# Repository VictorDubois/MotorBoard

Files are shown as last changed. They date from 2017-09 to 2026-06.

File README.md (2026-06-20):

Custom PCB for Krabi V1, to control DC motors using [LMD18200](https://www.ti.com/lit/ds/symlink/lmd18200.pdf)

MCU: [STM32 NUCLEO-G431KB](https://www.st.com/en/evaluation-tools/nucleo-g431kb.html), code is here https://github.com/VictorDubois/Motor-board-STM32-CAN/tree/commit-all

[Click for online viewer</br>
Capture d’écran du 2026-06-20 12-18-06](https://kicanvas.org/?repo=https%3A%2F%2Fgithub.com%2FVictorDubois%2FMotorBoard%2Ftree%2Fv2026.1%2F)

Note: Krabi V2 uses this PCB instead https://github.com/VictorDubois/CanMotorBoard

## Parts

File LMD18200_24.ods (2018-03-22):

Qty | Value | Device | Package | code RS | URL RS | prix unit HT RS (pour 3 boards) |  |  | Prix / carte | code RS particuliers
1 |  | MA03-2 | MA03-2 |  |  |  |  |  | 0
3 |  | MA06-1 | MA06-1 |  |  |  |  |  | 0
2 |  | MA08-1 | MA08-1 |  |  |  |  |  | 0
1 |  | MA10-2 | MA10-2 |  |  |  |  |  | 0
2 | 10k | R | R0805 | 707-7745 | http://fr.rs-online.com/web/p/resistances-traversantes/7077745/ | 0,006 |  |  | 0,015 | 707-7745
5 | 10k | R-EU_R0805 | R0805 | 125-1189 | http://fr.rs-online.com/web/p/resistances-cms/1251189/ | 0,002 | CRG0805F10K |  | 0,0125 | 707-7745
3 |  | W237-102 | W237-102 | 897-1262 + 897-1219 | http://fr.rs-online.com/web/p/borniers-pour-ci/8971262/ | 0,534 |  | + http://fr.rs-online.com/web/p/borniers-pour-ci/8971219/ | 2,0025 | 897-1262 + 897-1219
1 | 0R | R | R0805 | 125-1187 | http://fr.rs-online.com/web/p/resistances-cms/1251187/ | 0,002 | CRG0805ZR |  | 0,0025 | 901-3664
2 | 0R | R-EU_R0805 | R0805 | 125-1187 | http://fr.rs-online.com/web/p/resistances-cms/1251187/ | 0,002 | CRG0805ZR |  | 0,005 | 901-3664
2 | 1000mF | CPOL-EUE5-13 | E5-13 | 315-0754 | http://fr.rs-online.com/web/p/condensateurs-aluminium/3150754/ | 0,446 | EEUFC1V102 |  | 1,115 | 7111321
1 | 100nF | C-EUC0805 | C0805 | 264-4416 | http://fr.rs-online.com/web/p/condensateurs-ceramique-multicouche/2644416/ | 0,029 | C0805C104K5RACTU |  | 0,03625
6 | 100nF | C2.5/2 | C2.5-2 | 852-3273 | http://fr.rs-online.com/web/p/condensateurs-ceramique-multicouche/8523273/ | 0,02 | K104K15X7RF53L2 |  | 0,15 | 8523302 (https://www.rs-particuliers.com/WebCatalog/Condensateur_ceramique_multicouche_MLCC__Traversant__100nF___20___80__100V_dc__dielectrique__Y5V-8523302.aspx)
4 | 10nF | C2.5/2 | C2.5-2 | 264-4371 | http://fr.rs-online.com/web/p/condensateurs-ceramique-multicouche/2644371/ | 0,019 | C0805C103K5RACTU |  | 0,095 | 6994995 (https://www.rs-particuliers.com/WebCatalog/Condensateur_ceramique_multicouche_MLCC__Traversant__10nF__±20__100V_dc__dielectrique__Z5U-6994995.aspx)
1 | 30V | ZENER-DIODESOD80C | SOD80C |  |  |  |  |  | 0
2 | 330nF | C2.5/2 | C2.5-2 | 379-094 | http://fr.rs-online.com/web/p/condensateurs-ceramique-multicouche/0379094/ | 0,203 | FK24X7R1H334K |  | 0,5075 | 699-5153 (https://fr.rs-online.com/web/p/condensateurs-ceramique-multicouche/6995153/)
6 | 390 | R-EU_R0805 | R0805 | 679-1327 | http://fr.rs-online.com/web/p/resistances-cms/6791327/ | 0,009 | CRCW0805392RFKEA |  | 0,0675 | 679-1327
1 | 5V | ZENER-DIODESOD80C | SOD80C |  |  |  |  |  | 0
1 | 7406D | 7406D | SO14 | 662-7424 | http://fr.rs-online.com/web/p/buffers-et-drivers-de-ligne/6627424/ | 0,4 | SN7406DR |  | 0,5 | 662-7424
1 | 74HCT541DW | 74HCT541DW | SO20W | 177-6887 | http://fr.rs-online.com/web/p/buffers-et-drivers-de-ligne/1776887/ | 0,54 | 74HCT541D |  | 0,675 | 177-6887
1 | 7805TV | 7805TV | TO220V | 298-8508 | http://fr.rs-online.com/web/p/regulateurs-de-tension-lineaires/2988508/ | 0,29 | L7805ACV |  | 0,3625 | 298-8508
1 | ADC08032D | ADC08032D | SO08 | 669-6058 | http://fr.rs-online.com/web/p/can-a-usage-general/6696058/ | 1,615 | MCP3002-I/SN |  | 2,01875 | 669-6058 | Le 13/12/17
5 | HCPL2630 | HCPL2630 | DIL08 | 671-1419 | http://fr.rs-online.com/web/p/optocoupleurs/6711419/ | 2,07 | HCPL2630 |  | 12,9375 | 671-1419
2 | LM18200T | LM18200T | TO-220-11 | 534-4276 | http://fr.rs-online.com/web/p/drivers-de-moteur/5344276/ | 14,17 | LMD18200T/NOPB |  | 35,425 | 534-4276
4 | MOUNT-PAD-ROUND3.2 | MOUNT-PAD-ROUND3.2 | 3,2-PAD |  |  |  |  |  | 0
2 | NC | R-EU_R0805 | R0805 |  |  |  |  |  | 0
 |  |  |  |  |  |  |  |  | 55,9275

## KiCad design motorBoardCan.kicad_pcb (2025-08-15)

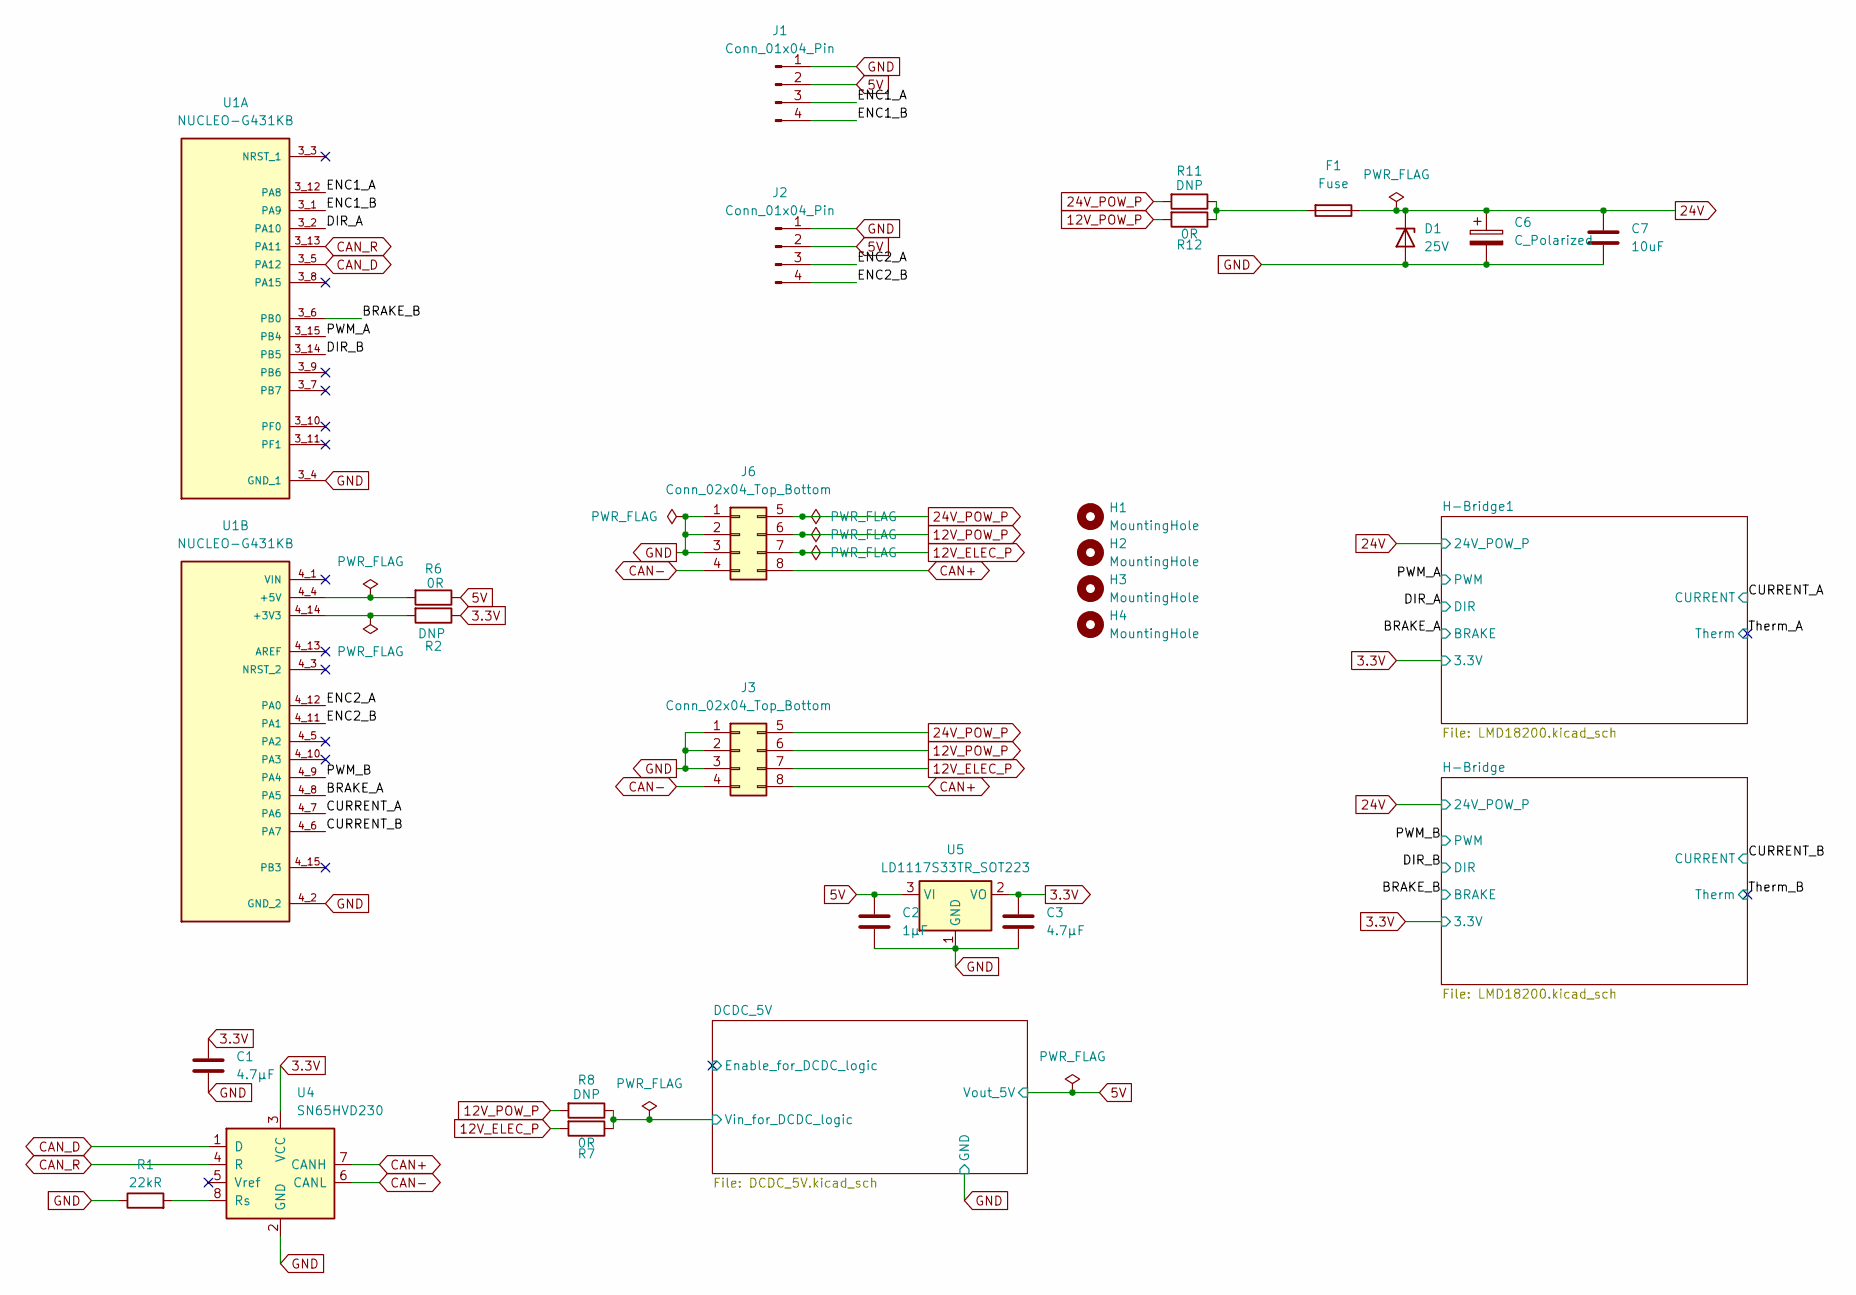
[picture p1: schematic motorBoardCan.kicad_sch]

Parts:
C1, C3: 4.7µF; C_1206_3216Metric; LCSC# C29823
C2: 1µF; C_1206_3216Metric; LCSC# C91151
C6: C_Polarized; CP_Radial_D10.0mm_P5.00mm; LCSC# C398835
C7: 10uF; C_0805_2012Metric; LCSC# C1713
D1: 25V; C_0805_2012Metric; LCSC# C118721
F1: Fuse; Fuse_Littelfuse-NANO2-451_453; LCSC# C27515
H1, H2, H3, H4: MountingHole; MountingHole_3.2mm_M3
J1, J2: Conn_01x04_Pin; PinHeader_1x04_P2.54mm_Vertical; LCSC# C2691448
J3, J6: Conn_02x04_Top_Bottom; Molex_Micro-Fit_3.0_43045-0812_2x04_P3.00mm_Vertical; LCSC# C277661
R1: 22kR; R_0603_1608Metric; LCSC# C2907128
R2, R8, R11: DNP; R_0603_1608Metric
R6, R7, R12: 0R; R_0603_1608Metric; LCSC# C21189
U1: NUCLEO-G431KB; MODULE_NUCLEO-G431KB
U4: SN65HVD230; SOIC-8_3.9x4.9mm_P1.27mm; LCSC# C12084
U5: LD1117S33TR_SOT223; SOT-223-3_TabPin2; LCSC# C20538890

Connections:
3.3V: C1.1, C3.1, R2.1, U4.3 (VCC), U5.2 (VO); also elsewhere on the board
5V: C2.1, J1.2, J2.2, R6.1, U5.3 (VI); also elsewhere on the board
12V_ELEC_P: J3.7, J6.7, R7.2
12V_POW_P: J3.6, J6.6, R8.2, R12.2
24V: C6.1, C7.1, D1.1 (K), F1.1; also elsewhere on the board
24V_POW_P: J3.5, J6.5, R11.2
/BRAKE_A: U1.4_8 (PA5); also elsewhere on the board
/BRAKE_B: U1.3_6 (PB0); also elsewhere on the board
/CURRENT_A: U1.4_7 (PA6); also elsewhere on the board
/CURRENT_B: U1.4_6 (PA7); also elsewhere on the board
/DCDC_5V/Vin_for_DCDC_logic: R7.1, R8.1; also elsewhere on the board
/DIR_A: U1.3_2 (PA10); also elsewhere on the board
/DIR_B: U1.3_14 (PB5); also elsewhere on the board
/ENC1_A: J1.3, U1.3_12 (PA8)
/ENC1_B: J1.4, U1.3_1 (PA9)
/ENC2_A: J2.3, U1.4_12 (PA0)
/ENC2_B: J2.4, U1.4_11 (PA1)
/PWM_A: U1.3_15 (PB4); also elsewhere on the board
/PWM_B: U1.4_9 (PA4); also elsewhere on the board
CAN+: J3.8, J6.8, U4.7 (CANH)
CAN-: J3.4, J6.4, U4.6 (CANL)
CAN_D: U1.3_5 (PA12), U4.1 (D)
CAN_R: U1.3_13 (PA11), U4.4 (R)
GND: C1.2, C2.2, C3.2, C6.2, C7.2, D1.2 (A), J1.1, J2.1, J3.1, J3.2, J3.3, J6.1, J6.2, J6.3, R1.1, U1.3_4 (GND_1), U1.4_2 (GND_2), U4.2 (GND), U5.1 (GND); also elsewhere on the board
unnamed: F1.2, R11.1, R12.1
unnamed: R2.2, U1.4_14 (+3V3)
unnamed: R6.2, U1.4_4 (+5V)
unnamed: R1.2, U4.8 (Rs)

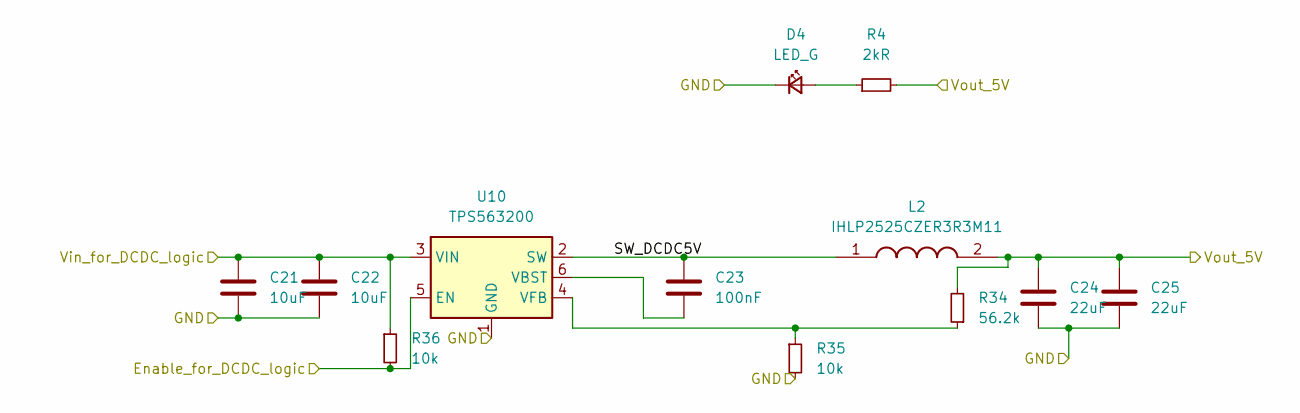
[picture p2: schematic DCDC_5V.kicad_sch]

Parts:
C21, C22: 10uF; C_0805_2012Metric; LCSC# C1713
C23: 100nF; C_0603_1608Metric; LCSC# C14663
C24, C25: 22uF; C_0805_2012Metric; LCSC# C5674
D4: LED_G; LED_0805_2012Metric; LCSC# C965815
L2: IHLP2525CZER3R3M11; INDPM6965X300N; Mouser Part Number 70-IHLP2525CZER3R3M1
R4: 2kR; R_0603_1608Metric; LCSC# C2907137
R34: 56.2k; C_0603_1608Metric; LCSC# C2930117
R35, R36: 10k; C_0603_1608Metric; LCSC# C2930027
U10: TPS563200; SOT-23-6; LCSC# C97253

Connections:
5V: C24.1, C25.1, L2.2, R4.2, R34.2; also elsewhere on the board
/DCDC_5V/Enable_for_DCDC_logic: R36.2, U10.5 (EN)
/DCDC_5V/SW_DCDC5V: C23.1, L2.1, U10.2 (SW)
/DCDC_5V/Vin_for_DCDC_logic: C21.1, C22.1, R36.1, U10.3 (VIN); also elsewhere on the board
GND: C21.2, C22.2, C24.2, C25.2, D4.1 (K), R35.2, U10.1 (GND); also elsewhere on the board
unnamed: D4.2 (A), R4.1
unnamed: C23.2, U10.6 (VBST)
unnamed: R34.1, R35.1, U10.4 (VFB)

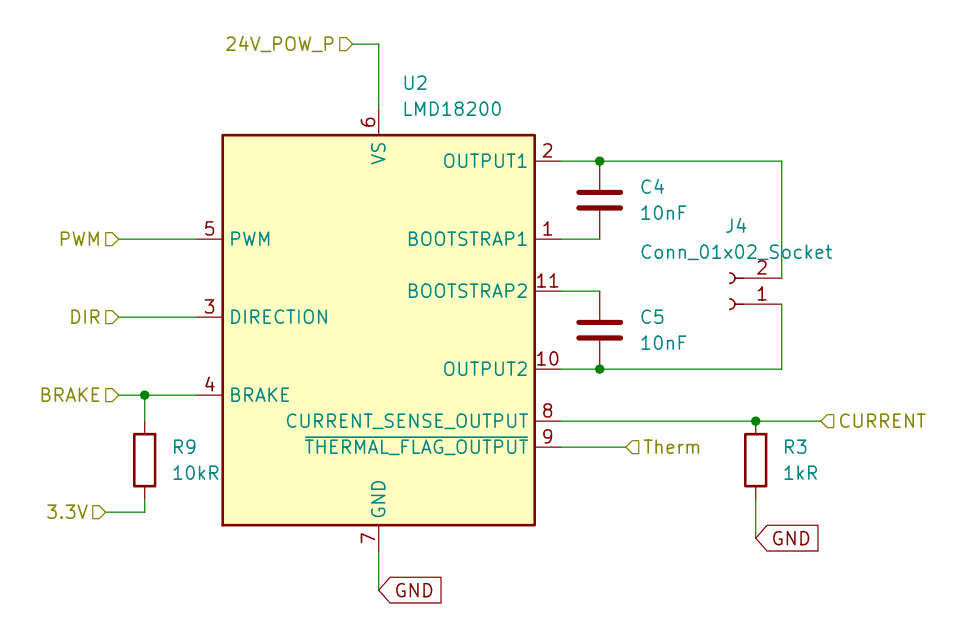
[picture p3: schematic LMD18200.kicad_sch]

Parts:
C4, C5: 10nF; C_0603_1608Metric; LCSC# C57112
J4: Conn_01x02_Socket; PhoenixContact_MC_1,5_2-G-3.81_1x02_P3.81mm_Horizontal
R3: 1kR; R_0603_1608Metric; LCSC# C2907113
R9: 10kR; R_0603_1608Metric; LCSC# C2907113
U2: LMD18200; TO-220-11_P3.4x5.08mm_StaggerOdd_Lead4.85mm_Vertical; LCSC# C117011

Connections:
3.3V: R9.1; also elsewhere on the board
24V: U2.6 (VS); also elsewhere on the board
/BRAKE_B: R9.2, U2.4 (BRAKE); also elsewhere on the board
/CURRENT_B: R3.2, U2.8 (CURRENT_SENSE_OUTPUT); also elsewhere on the board
/DIR_B: U2.3 (DIRECTION); also elsewhere on the board
/PWM_B: U2.5 (PWM); also elsewhere on the board
/Therm_B: U2.9 (~THERMAL_FLAG_OUTPUT)
GND: R3.1, U2.7 (GND); also elsewhere on the board
unnamed: C5.2, J4.1, U2.10 (OUTPUT2)
unnamed: C4.1, J4.2, U2.2 (OUTPUT1)
unnamed: C4.2, U2.1 (BOOTSTRAP1)
unnamed: C5.1, U2.11 (BOOTSTRAP2)

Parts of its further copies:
C8, C9: 10nF; C_0603_1608Metric; LCSC# C57112
J5: Conn_01x02_Socket; PhoenixContact_MC_1,5_2-G-3.81_1x02_P3.81mm_Horizontal
R5: 1kR; R_0603_1608Metric; LCSC# C2907113
R10: 10kR; R_0603_1608Metric; LCSC# C2907113
U6: LMD18200; TO-220-11_P3.4x5.08mm_StaggerOdd_Lead4.85mm_Vertical; LCSC# C117011

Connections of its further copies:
3.3V: R10.1; also elsewhere on the board
24V: U6.6 (VS); also elsewhere on the board
/BRAKE_A: R10.2, U6.4 (BRAKE); also elsewhere on the board
/CURRENT_A: R5.2, U6.8 (CURRENT_SENSE_OUTPUT); also elsewhere on the board
/DIR_A: U6.3 (DIRECTION); also elsewhere on the board
/PWM_A: U6.5 (PWM); also elsewhere on the board
/Therm_A: U6.9 (~THERMAL_FLAG_OUTPUT)
GND: R5.1, U6.7 (GND); also elsewhere on the board
unnamed: C9.2, J5.1, U6.10 (OUTPUT2)
unnamed: C8.1, J5.2, U6.2 (OUTPUT1)
unnamed: C8.2, U6.1 (BOOTSTRAP1)
unnamed: C9.1, U6.11 (BOOTSTRAP2)

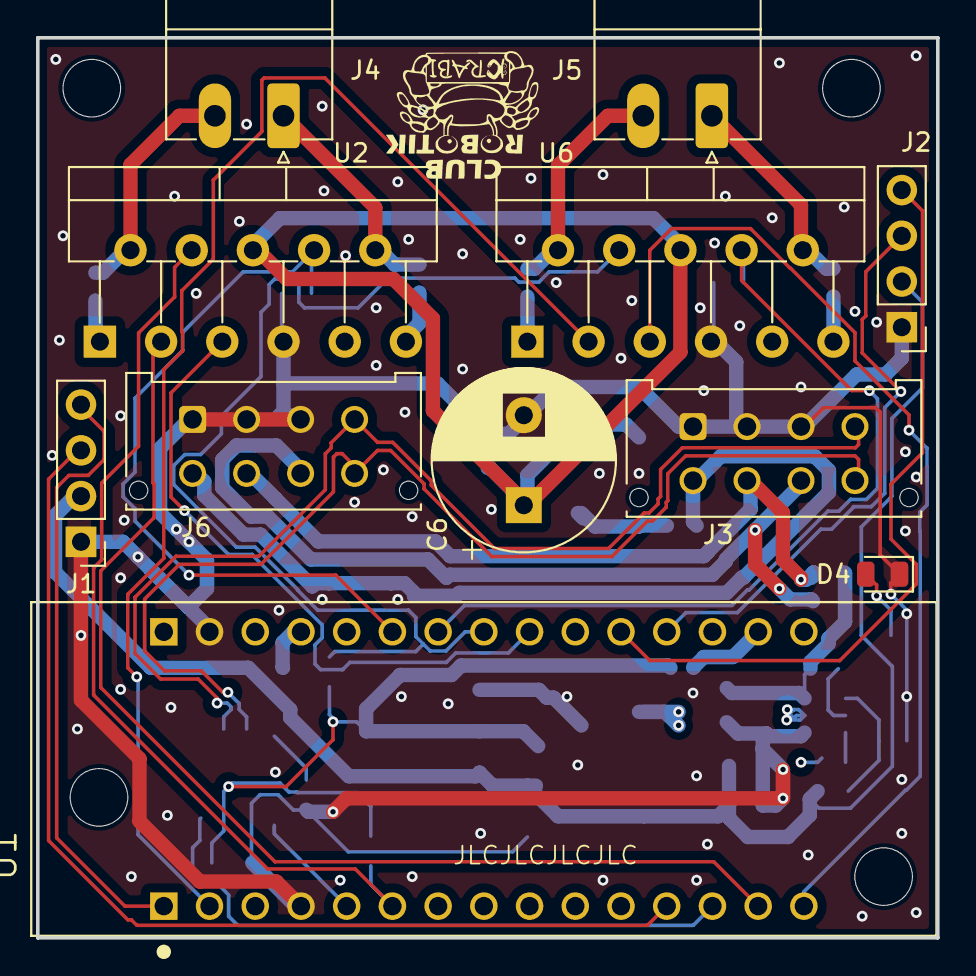
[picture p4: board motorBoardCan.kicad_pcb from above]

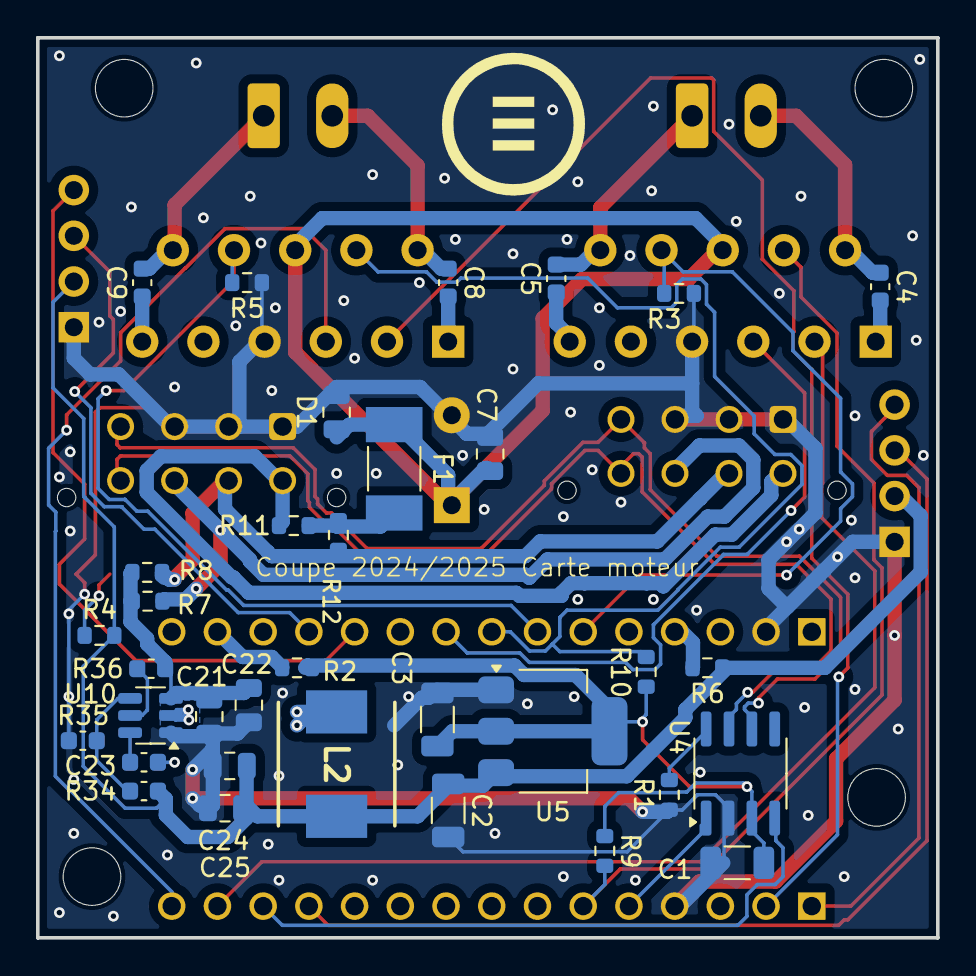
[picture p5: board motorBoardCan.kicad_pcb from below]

Board: 6 copper layers, 50.0 x 50.0 mm, 49 parts (34 on the bottom side), 41 nets.

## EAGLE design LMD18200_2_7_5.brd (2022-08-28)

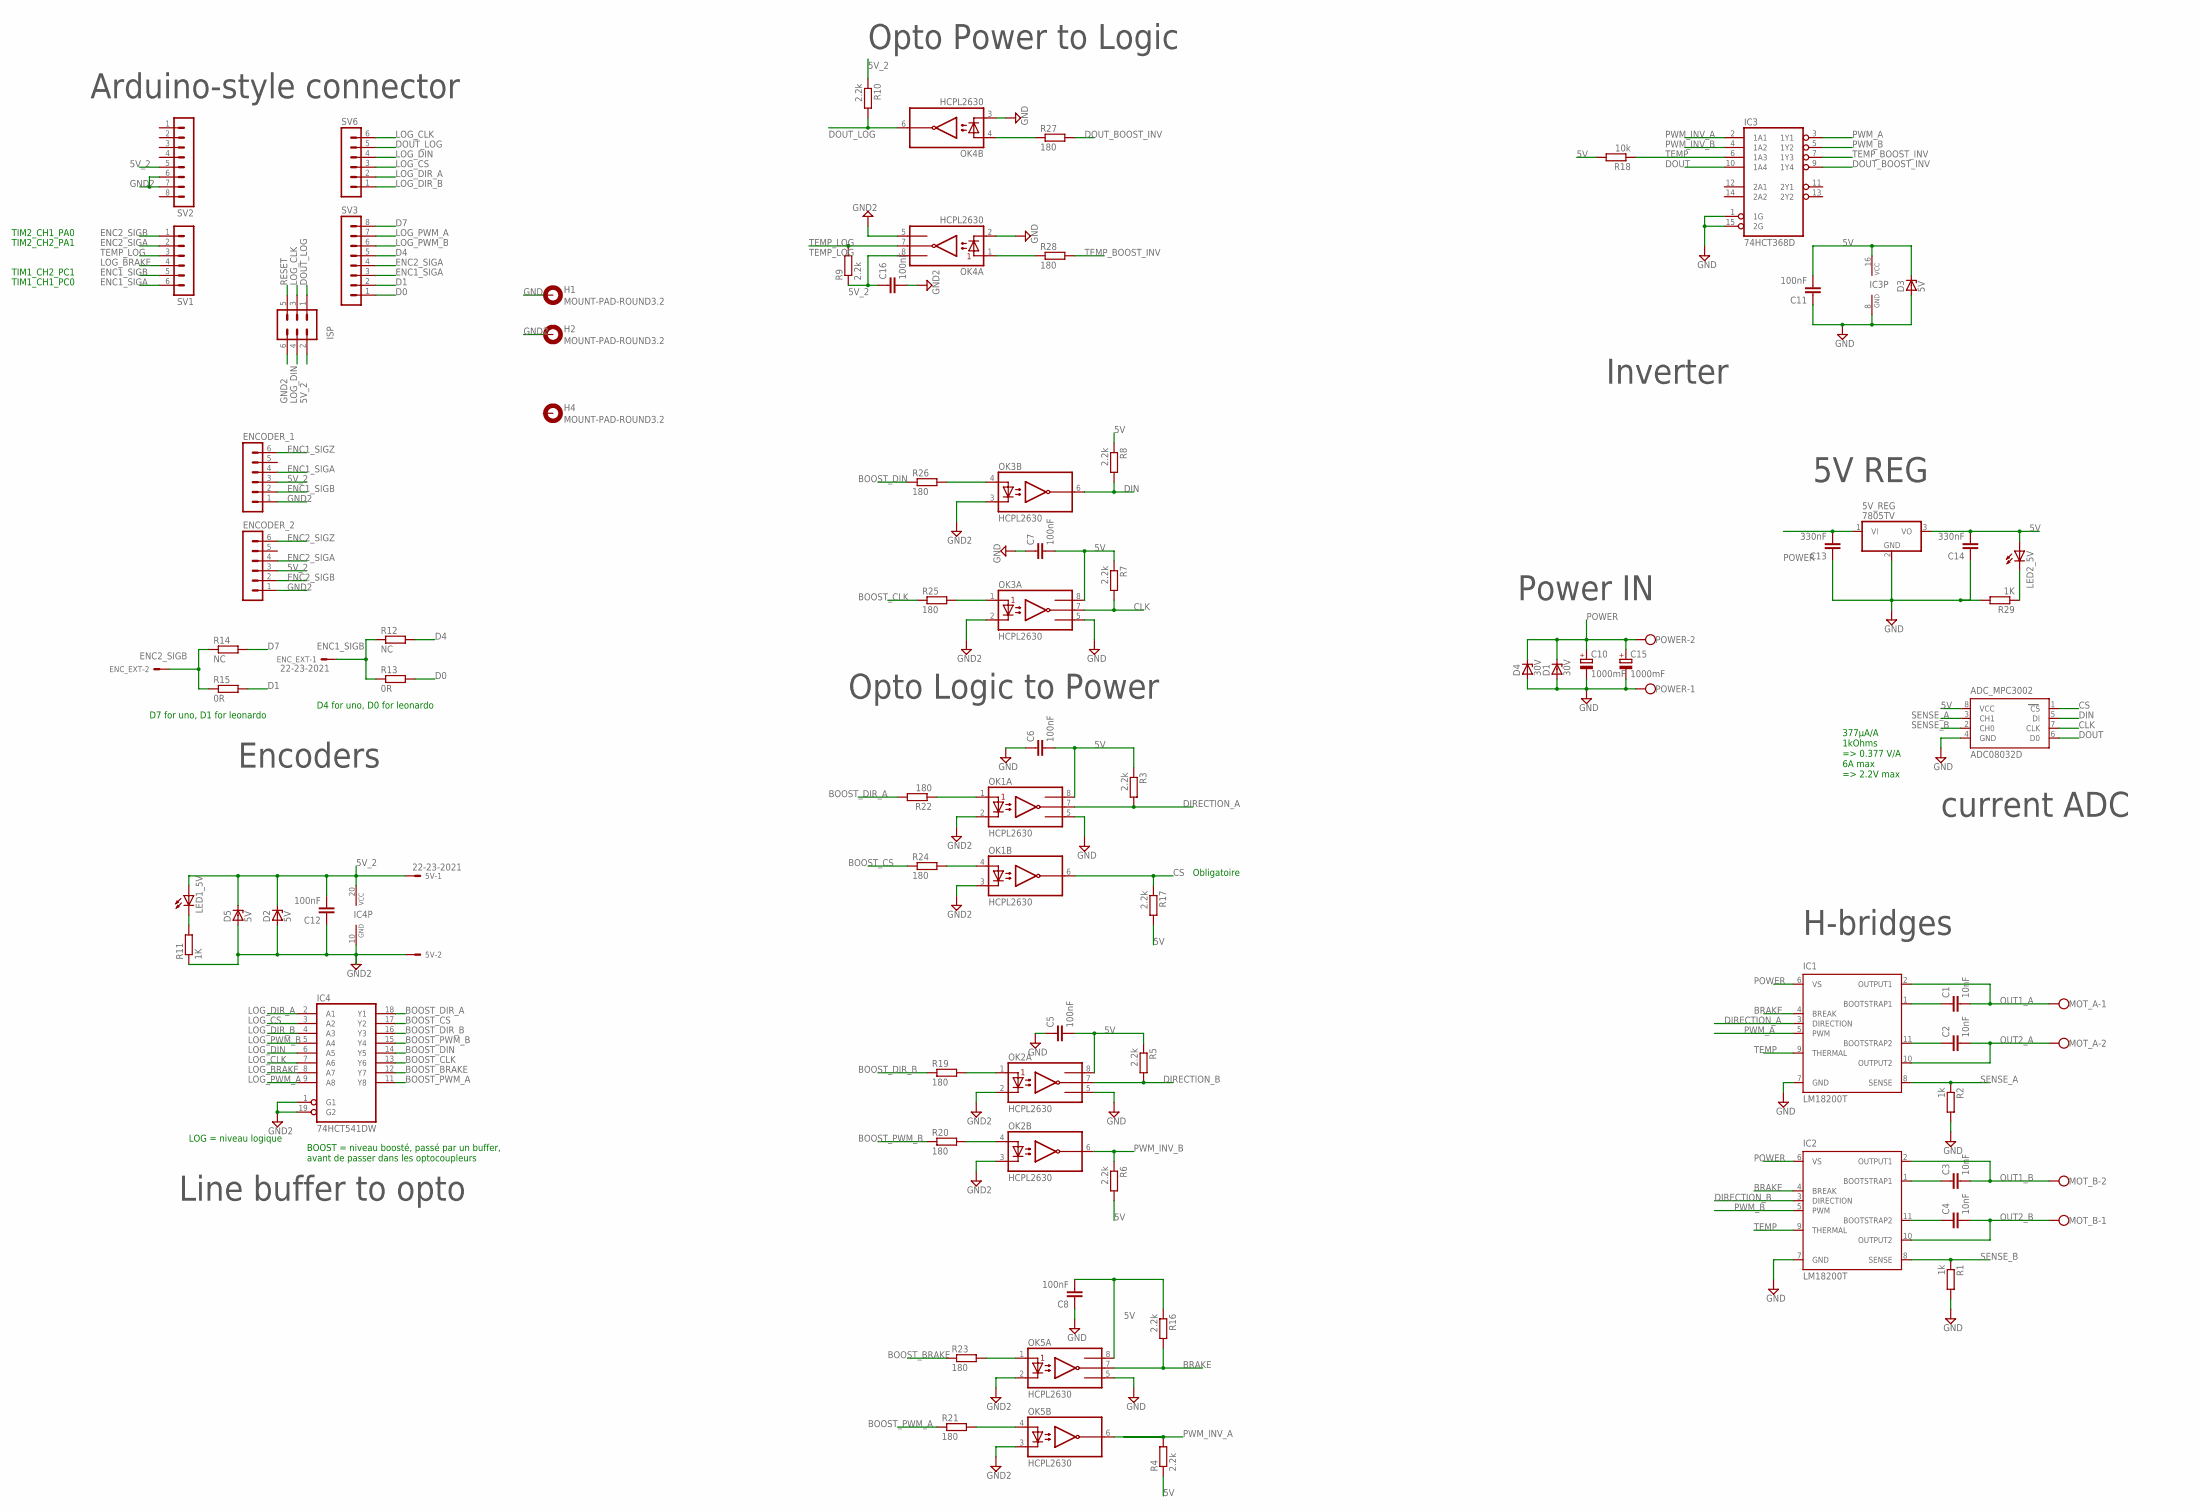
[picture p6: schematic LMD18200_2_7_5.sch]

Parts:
5V: 22-23-2021
5V_REG: 7805TV; TO220V
ADC_MPC3002: ADC08032D; SO08
C1, C2, C3, C4: 10nF; C0603
C5, C6, C7, C8, C12, C16: 100nF; C0603
C10, C15: 1000mF; E5-13
C11: 100nF; C0805
C13, C14: 330nF; C0603
D1: 30V; SOD80C
D2: 5V; SOD80C
D3, D5: 5V; DO34Z7
D4: 30V; DO34Z7
ENCODER_1, ENCODER_2: MA06-1
ENC_EXT: 22-23-2021
H1, H2, H4: MOUNT-PAD-ROUND3.2; 3,2-PAD
IC1, IC2: LM18200T; TO-220-11
IC3: 74HCT368D; SO16
IC4: 74HCT541DW; SO20W
ISP: MA03-2
LED1_5V, LED2_5V: LEDSML0805; SML0805
MOT_A: W237-102
MOT_B: W237-102
OK1, OK2, OK3, OK4, OK5: HCPL2630; DIL08
POWER: W237-102
R1, R2: 1k; R0603
R3, R4, R5, R6, R7, R8, R9, R10, R16, R17: 2.2k; R0603
R11, R29: 1K; R0603
R12, R14: NC; R0603
R13, R15: 0R; R0603
R18: 10k; R0603
R19, R20, R21, R22, R23, R24, R25, R26, R27, R28: 180; R0603
SV1, SV6: MA06-1
SV2, SV3: MA08-1

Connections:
5V: 5V_REG.3 (VO), ADC_MPC3002.8 (VCC), C5.2, C6.2, C7.2, C8.2, C11.2, C14.2, D3.C, IC3.16 (VCC), LED2_5V.A, OK1.8 (VCC), OK2.8 (VCC), OK3.8 (VCC), OK5.8 (VCC), R3.1, R4.1, R5.1, R6.2, R7.1, R8.1, R16.1, R17.2, R18.2
5V_2: 5V.1, C12.2, C16.1, D2.C, D5.C, ENCODER_1.3, ENCODER_2.3, IC4.20 (VCC), ISP.2, LED1_5V.A, OK4.8 (VCC), R9.1, R10.1, SV2.5
BOOST_BRAKE: IC4.12 (Y7), R23.1
BOOST_CLK: IC4.13 (Y6), R25.1
BOOST_CS: IC4.17 (Y2), R24.1
BOOST_DIN: IC4.14 (Y5), R26.1
BOOST_DIR_A: IC4.18 (Y1), R22.2
BOOST_DIR_B: IC4.16 (Y3), R19.1
BOOST_OUT1_A: C1.1, IC1.1 (BOOTSTRAP1)
BOOST_OUT1_B: C3.1, IC2.1 (BOOTSTRAP1)
BOOST_OUT2_A: C2.1, IC1.11 (BOOTSTRAP2)
BOOST_OUT2_B: C4.1, IC2.11 (BOOTSTRAP2)
BOOST_PWM_A: IC4.11 (Y8), R21.1
BOOST_PWM_B: IC4.15 (Y4), R20.1
BRAKE: IC1.4 (BREAK), IC2.4 (BREAK), OK5.7 (VO1), R16.2
CLK: ADC_MPC3002.7 (CLK), OK3.7 (VO1), R7.2
CS: ADC_MPC3002.1 (CS), OK1.6 (VO2), R17.1
D0: R13.2, SV3.1
D1: R15.2, SV3.2
D4: R12.2, SV3.5
D7: R14.2, SV3.8
DIN: ADC_MPC3002.5 (DI), OK3.6 (VO2), R8.2
DIRECTION_A: IC1.3 (DIRECTION), OK1.7 (VO1), R3.2
DIRECTION_B: IC2.3 (DIRECTION), OK2.7 (VO1), R5.2
DOUT: ADC_MPC3002.6 (D0), IC3.10 (1A4)
DOUT_BOOST_INV: IC3.9 (1Y4), R27.2
DOUT_LOG: ISP.1, OK4.6 (VO2), R10.2, SV6.5
ENC1_SIGA: ENCODER_1.4, SV1.6, SV3.3
ENC1_SIGB: ENCODER_1.2, ENC_EXT.1, R12.1, R13.1, SV1.5
ENC1_SIGZ: ENCODER_1.6
ENC2_SIGA: ENCODER_2.4, SV1.2, SV3.4
ENC2_SIGB: ENCODER_2.2, ENC_EXT.2, R14.1, R15.1, SV1.1
ENC2_SIGZ: ENCODER_2.6
GND: 5V_REG.2 (GND), ADC_MPC3002.4 (GND), C5.1, C6.1, C7.1, C8.1, C10.-, C11.1, C13.1, C14.1, C15.-, D1.A, D3.A, D4.A, H1.B3,2, IC1.7 (GND), IC2.7 (GND), IC3.1 (1G), IC3.8 (GND), IC3.15 (2G), OK1.5 (GND), OK2.5 (GND), OK3.5 (GND), OK4.2 (C1), OK4.3 (C2), OK5.5 (GND), POWER.1, R1.2, R2.2, R29.2
GND2: 5V.2, C12.1, C16.2, D2.A, D5.A, ENCODER_1.1, ENCODER_2.1, H2.B3,2, IC4.1 (G1), IC4.10 (GND), IC4.19 (G2), ISP.6, OK1.2 (C1), OK1.3 (C2), OK2.2 (C1), OK2.3 (C2), OK3.2 (C1), OK3.3 (C2), OK4.5 (GND), OK5.2 (C1), OK5.3 (C2), R11.1, SV2.6, SV2.7
LED1_SIG: LED1_5V.C, R11.2
LED2_5V_SIG: LED2_5V.C, R29.1
LOG_BRAKE: IC4.8 (A7), SV1.4
LOG_CLK: IC4.7 (A6), ISP.3, SV6.6
LOG_CS: IC4.3 (A2), SV6.3
LOG_DIN: IC4.6 (A5), ISP.4, SV6.4
LOG_DIR_A: IC4.2 (A1), SV6.2
LOG_DIR_B: IC4.4 (A3), SV6.1
LOG_PWM_A: IC4.9 (A8), SV3.7
LOG_PWM_B: IC4.5 (A4), SV3.6
OUT1_A: C1.2, IC1.2 (OUTPUT1), MOT_A.1
OUT1_B: C3.2, IC2.2 (OUTPUT1), MOT_B.2
OUT2_A: C2.2, IC1.10 (OUTPUT2), MOT_A.2
OUT2_B: C4.2, IC2.10 (OUTPUT2), MOT_B.1
POWER: 5V_REG.1 (VI), C10.+, C13.2, C15.+, D1.C, D4.C, IC1.6 (VS), IC2.6 (VS), POWER.2
PWM_A: IC1.5 (PWM), IC3.3 (1Y1)
PWM_B: IC2.5 (PWM), IC3.5 (1Y2)
PWM_INV_A: IC3.2 (1A1), OK5.6 (VO2), R4.2
PWM_INV_B: IC3.4 (1A2), OK2.6 (VO2), R6.1
RESET: ISP.5
R_BOOST_BRAKE: OK5.1 (A1), R23.2
R_BOOST_CLK: OK3.1 (A1), R25.2
R_BOOST_CS: OK1.4 (A2), R24.2
R_BOOST_DIN: OK3.4 (A2), R26.2
R_BOOST_DIR_A: OK1.1 (A1), R22.1
R_BOOST_DIR_B: OK2.1 (A1), R19.2
R_BOOST_PWM_A: OK5.4 (A2), R21.2
R_BOOST_PWM_B: OK2.4 (A2), R20.2
R_DOUT_BOOST_INV: OK4.4 (A2), R27.1
R_TEMP_BOOST_INV: OK4.1 (A1), R28.1
SENSE_A: ADC_MPC3002.3 (CH1), IC1.8 (SENSE), R2.1
SENSE_B: ADC_MPC3002.2 (CH0), IC2.8 (SENSE), R1.1
TEMP: IC1.9 (THERMAL), IC2.9 (THERMAL), IC3.6 (1A3), R18.1
TEMP_BOOST_INV: IC3.7 (1Y3), R28.2
TEMP_LOG: OK4.7 (VO1), R9.2, SV1.3

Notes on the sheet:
D4 for uno, D0 for leonardo
D7 for uno, D1 for leonardo
LOG = niveau logique
BOOST = niveau boosté, passé par un buffer, avant de passer dans les optocoupleurs
Obligatoire
H-bridges
current ADC
TIM1_CH1_PC0
TIM1_CH2_PC1
TIM2_CH2_PA1
TIM2_CH1_PA0
377µA/A 1kOhms => 0.377 V/A 6A max => 2.2V max
5V REG
Power IN
Inverter
Opto Power to Logic
Opto Logic to Power
Arduino-style connector
Encoders
Line buffer to opto

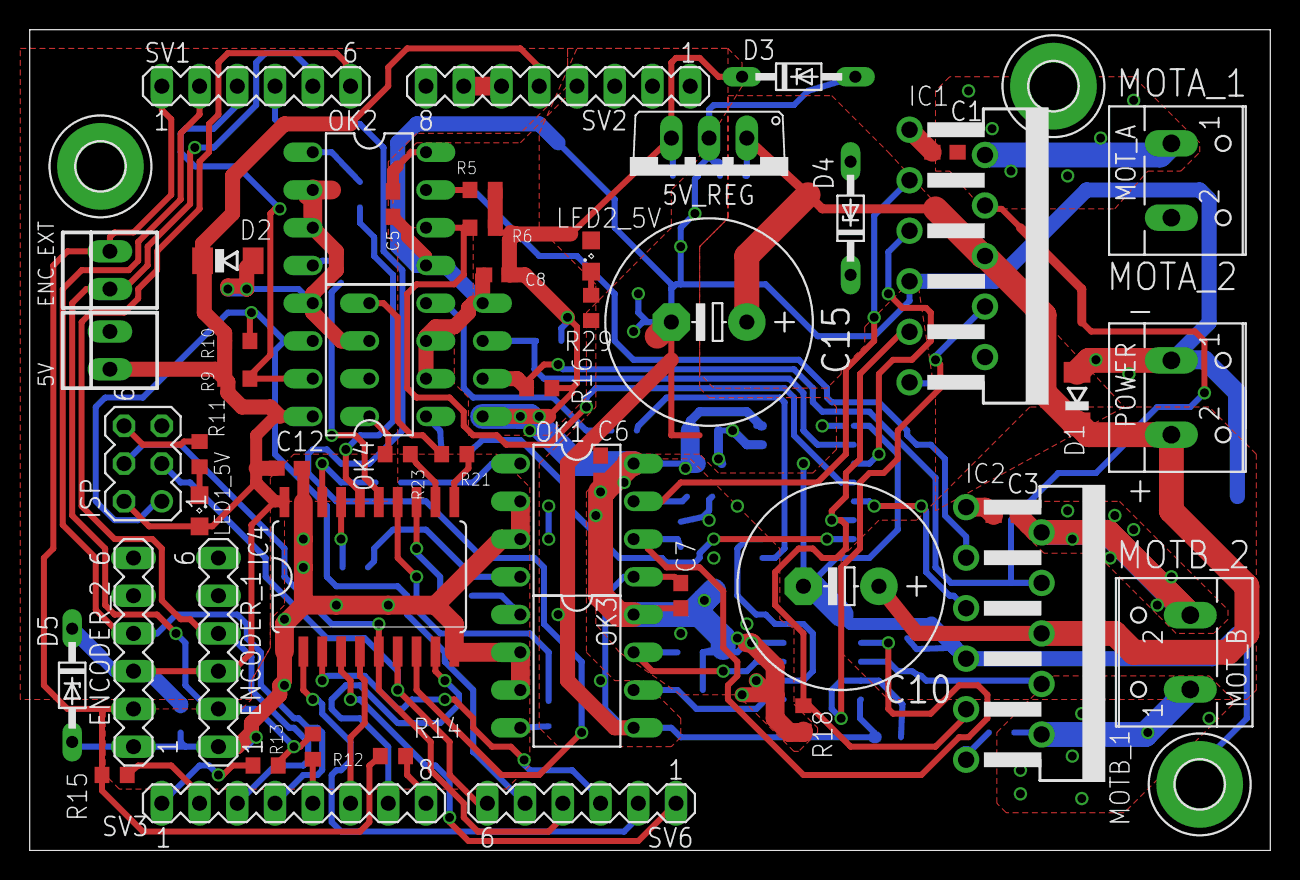
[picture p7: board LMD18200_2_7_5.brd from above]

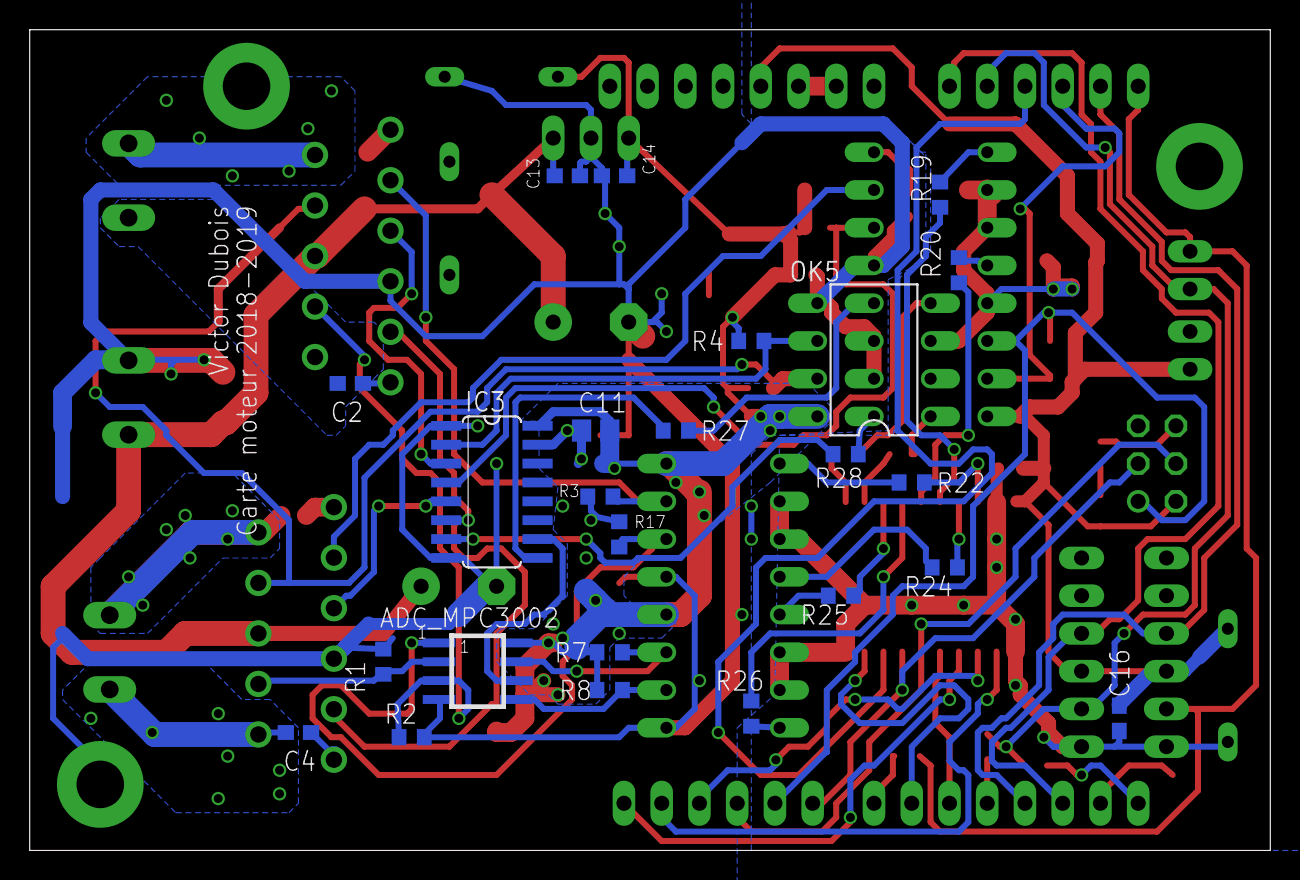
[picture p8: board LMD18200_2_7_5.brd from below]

Board: 2 copper layers, 83.5 x 55.2 mm, 77 parts (24 on the bottom side), 67 nets.

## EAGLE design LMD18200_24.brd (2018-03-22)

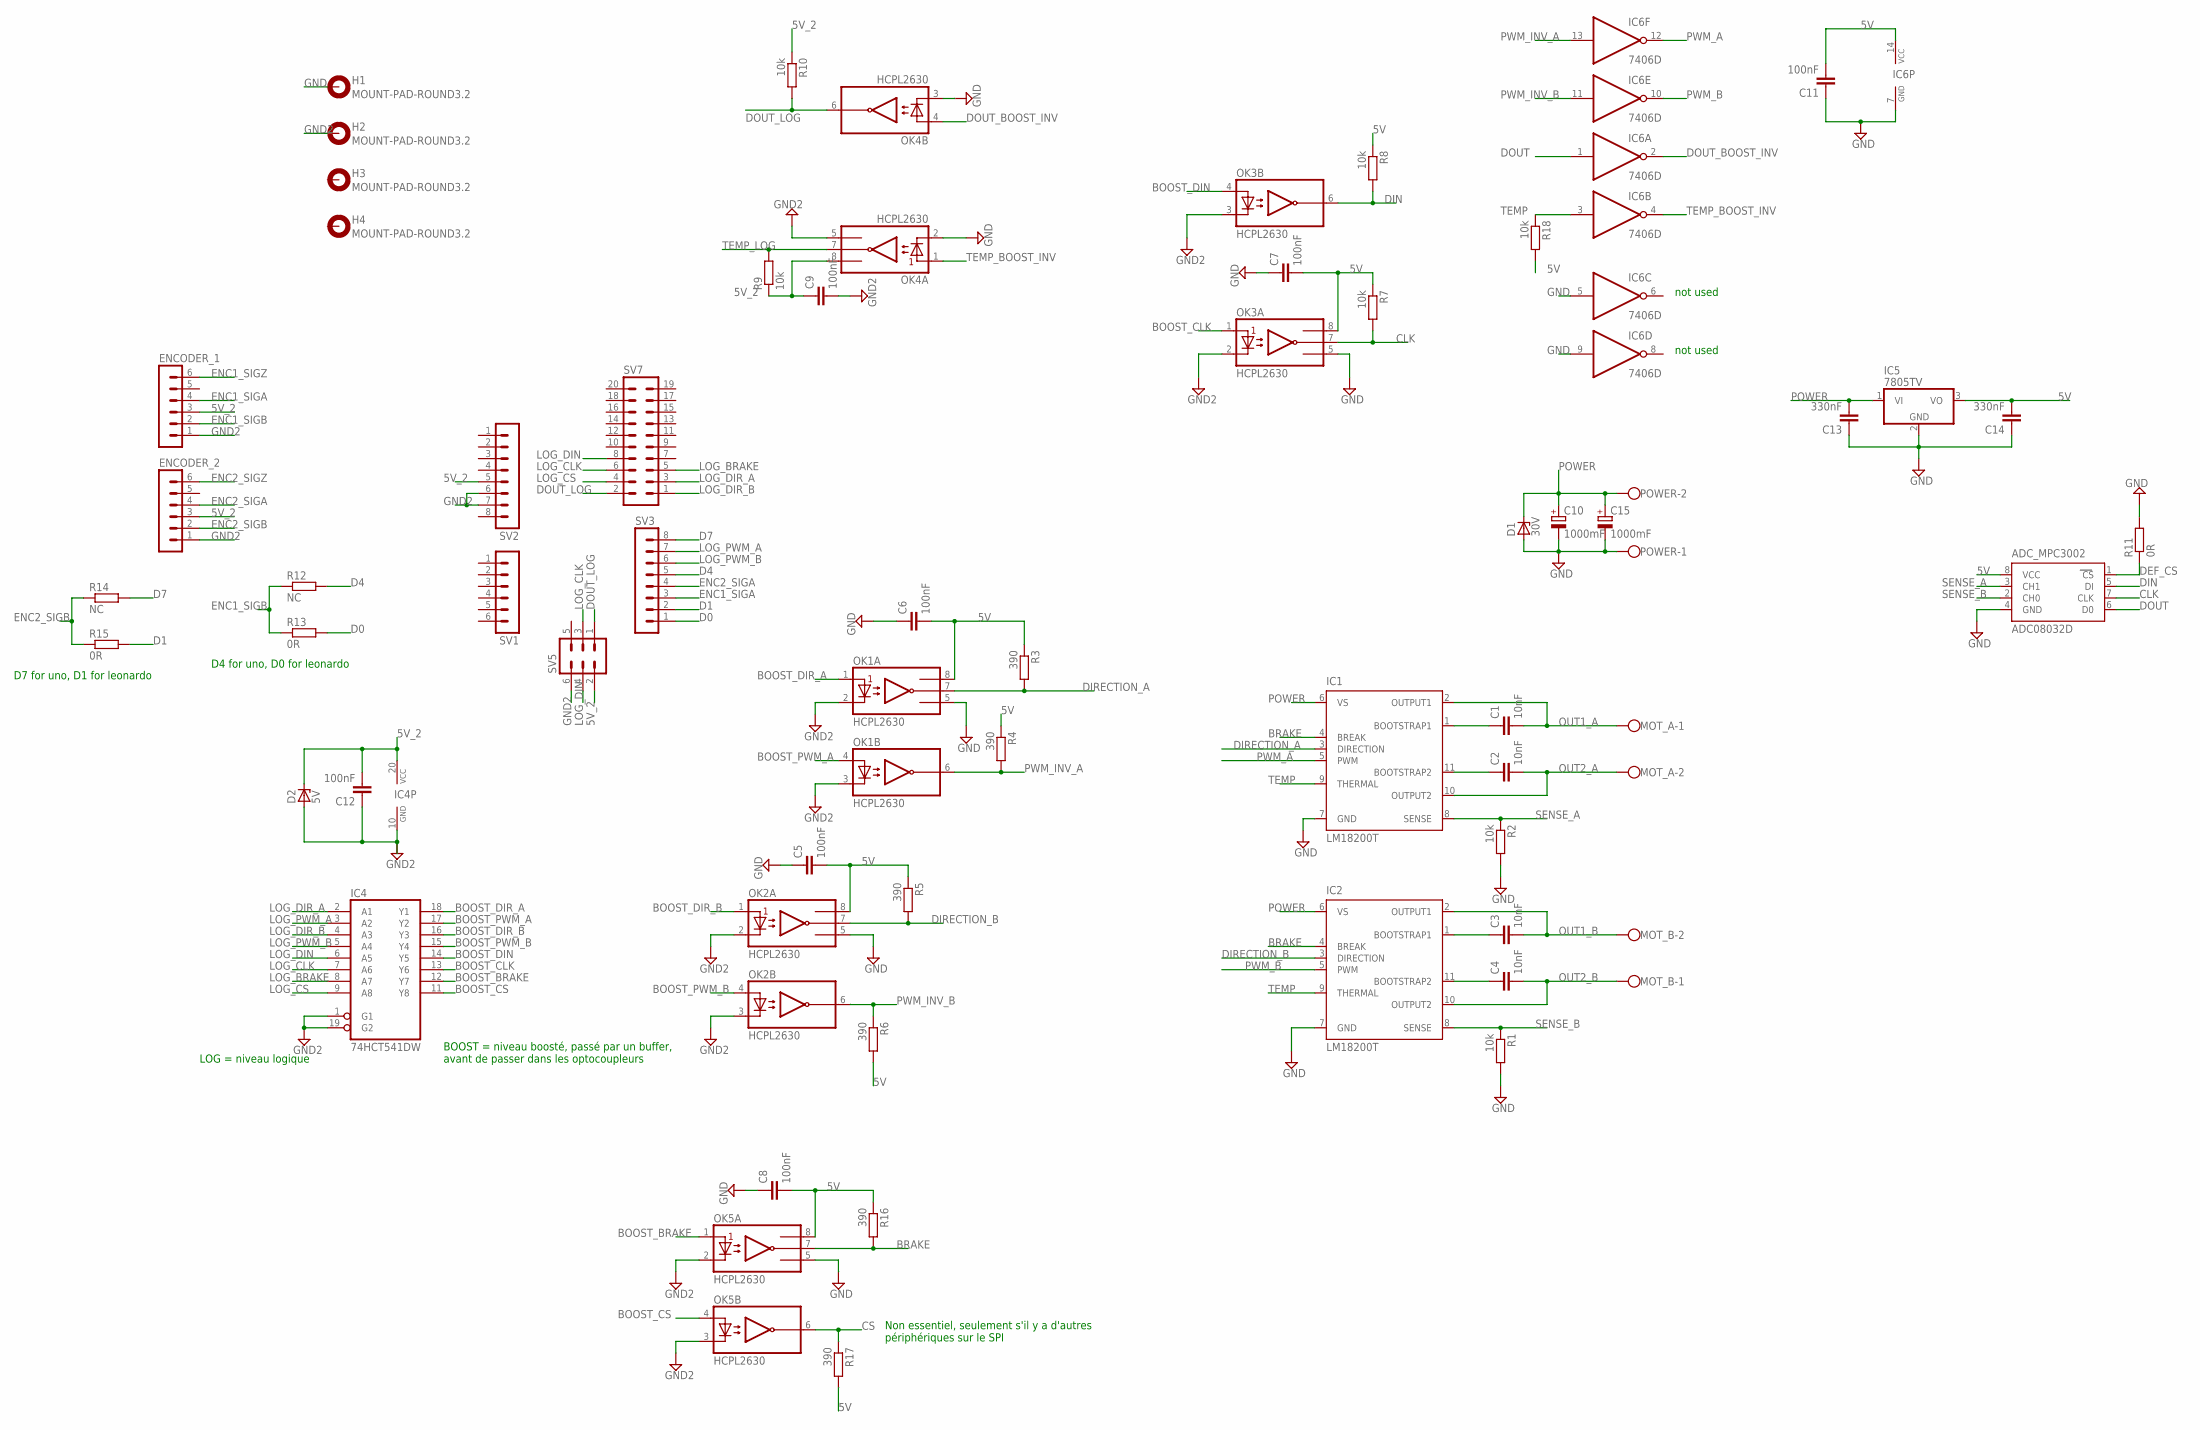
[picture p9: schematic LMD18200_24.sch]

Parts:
ADC_MPC3002: ADC08032D; SO08
C1, C2, C3, C4: 10nF; C2.5-2
C5, C6, C7, C8, C9, C12: 100nF; C2.5-2
C10, C15: 1000mF; E5-13
C11: 100nF; C0805
C13, C14: 330nF; C2.5-2
D1: 30V; SOD80C
D2: 5V; SOD80C
ENCODER_1, ENCODER_2: MA06-1
H1, H2, H3, H4: MOUNT-PAD-ROUND3.2; 3,2-PAD
IC1, IC2: LM18200T; TO-220-11
IC4: 74HCT541DW; SO20W
IC5: 7805TV; TO220V
IC6: 7406D; SO14
MOT_A: W237-102
MOT_B: W237-102
OK1, OK2, OK3, OK4, OK5: HCPL2630; DIL08
POWER: W237-102
R1, R2, R7, R8, R9, R10, R18: 10k; R0805
R3, R4, R5, R6, R16, R17: 390; R0805
R11, R13, R15: 0R; R0805
R12, R14: NC; R0805
SV1: MA06-1
SV2, SV3: MA08-1
SV5: MA03-2
SV7: MA10-2

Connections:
5V: ADC_MPC3002.8 (VCC), C5.2, C6.2, C7.2, C8.2, C11.2, C14.2, IC5.3 (VO), IC6.14 (VCC), OK1.8 (VCC), OK2.8 (VCC), OK3.8 (VCC), OK5.8 (VCC), R3.1, R4.1, R5.1, R6.2, R7.1, R8.1, R16.1, R17.2, R18.2
5V_2: C9.1, C12.2, D2.C, ENCODER_1.3, ENCODER_2.3, IC4.20 (VCC), OK4.8 (VCC), R9.1, R10.1, SV2.5, SV5.2
BOOST_BRAKE: IC4.12 (Y7), OK5.1 (A1)
BOOST_CLK: IC4.13 (Y6), OK3.1 (A1)
BOOST_CS: IC4.11 (Y8), OK5.4 (A2)
BOOST_DIN: IC4.14 (Y5), OK3.4 (A2)
BOOST_DIR_A: IC4.18 (Y1), OK1.1 (A1)
BOOST_DIR_B: IC4.16 (Y3), OK2.1 (A1)
BOOST_PWM_A: IC4.17 (Y2), OK1.4 (A2)
BOOST_PWM_B: IC4.15 (Y4), OK2.4 (A2)
BRAKE: IC1.4 (BREAK), IC2.4 (BREAK), OK5.7 (VO1), R16.2
CLK: ADC_MPC3002.7 (CLK), OK3.7 (VO1), R7.2
CS: OK5.6 (VO2), R17.1
D0: R13.2, SV3.1
D1: R15.2, SV3.2
D4: R12.2, SV3.5
D7: R14.2, SV3.8
DEF_CS: ADC_MPC3002.1 (CS), R11.1
DIN: ADC_MPC3002.5 (DI), OK3.6 (VO2), R8.2
DIRECTION_A: IC1.3 (DIRECTION), OK1.7 (VO1), R3.2
DIRECTION_B: IC2.3 (DIRECTION), OK2.7 (VO1), R5.2
DOUT: ADC_MPC3002.6 (D0), IC6.1 (I)
DOUT_BOOST_INV: IC6.2 (O), OK4.4 (A2)
DOUT_LOG: OK4.6 (VO2), R10.2, SV5.1, SV7.2
ENC1_SIGA: ENCODER_1.4, SV3.3
ENC1_SIGB: ENCODER_1.2, R12.1, R13.1
ENC1_SIGZ: ENCODER_1.6
ENC2_SIGA: ENCODER_2.4, SV3.4
ENC2_SIGB: ENCODER_2.2, R14.1, R15.1
ENC2_SIGZ: ENCODER_2.6
GND: ADC_MPC3002.4 (GND), C5.1, C6.1, C7.1, C8.1, C10.-, C11.1, C13.1, C14.1, C15.-, D1.A, H1.B3,2, IC1.7 (GND), IC2.7 (GND), IC5.2 (GND), IC6.5 (I), IC6.7 (GND), IC6.9 (I), OK1.5 (GND), OK2.5 (GND), OK3.5 (GND), OK4.2 (C1), OK4.3 (C2), OK5.5 (GND), POWER.1, R1.2, R2.2, R11.2
GND2: C9.2, C12.1, D2.A, ENCODER_1.1, ENCODER_2.1, H2.B3,2, IC4.1 (G1), IC4.10 (GND), IC4.19 (G2), OK1.2 (C1), OK1.3 (C2), OK2.2 (C1), OK2.3 (C2), OK3.2 (C1), OK3.3 (C2), OK4.5 (GND), OK5.2 (C1), OK5.3 (C2), SV2.6, SV2.7, SV5.6
LOG_BRAKE: IC4.8 (A7), SV7.5
LOG_CLK: IC4.7 (A6), SV5.3, SV7.6
LOG_CS: IC4.9 (A8), SV7.4
LOG_DIN: IC4.6 (A5), SV5.4, SV7.8
LOG_DIR_A: IC4.2 (A1), SV7.3
LOG_DIR_B: IC4.4 (A3), SV7.1
LOG_PWM_A: IC4.3 (A2), SV3.7
LOG_PWM_B: IC4.5 (A4), SV3.6
unnamed: C1.1, IC1.1 (BOOTSTRAP1)
unnamed: C2.1, IC1.11 (BOOTSTRAP2)
unnamed: C3.1, IC2.1 (BOOTSTRAP1)
unnamed: C4.1, IC2.11 (BOOTSTRAP2)
OUT1_A: C1.2, IC1.2 (OUTPUT1), MOT_A.1
OUT1_B: C3.2, IC2.2 (OUTPUT1), MOT_B.2
OUT2_A: C2.2, IC1.10 (OUTPUT2), MOT_A.2
OUT2_B: C4.2, IC2.10 (OUTPUT2), MOT_B.1
POWER: C10.+, C13.2, C15.+, D1.C, IC1.6 (VS), IC2.6 (VS), IC5.1 (VI), POWER.2
PWM_A: IC1.5 (PWM), IC6.12 (O)
PWM_B: IC2.5 (PWM), IC6.10 (O)
PWM_INV_A: IC6.13 (I), OK1.6 (VO2), R4.2
PWM_INV_B: IC6.11 (I), OK2.6 (VO2), R6.1
SENSE_A: ADC_MPC3002.3 (CH1), IC1.8 (SENSE), R2.1
SENSE_B: ADC_MPC3002.2 (CH0), IC2.8 (SENSE), R1.1
TEMP: IC1.9 (THERMAL), IC2.9 (THERMAL), IC6.3 (I), R18.1
TEMP_BOOST_INV: IC6.4 (O), OK4.1 (A1)
TEMP_LOG: OK4.7 (VO1), R9.2

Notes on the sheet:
D4 for uno, D0 for leonardo
D7 for uno, D1 for leonardo
LOG = niveau logique
BOOST = niveau boosté, passé par un buffer, avant de passer dans les optocoupleurs
Non essentiel, seulement s'il y a d'autres périphériques sur le SPI
not used

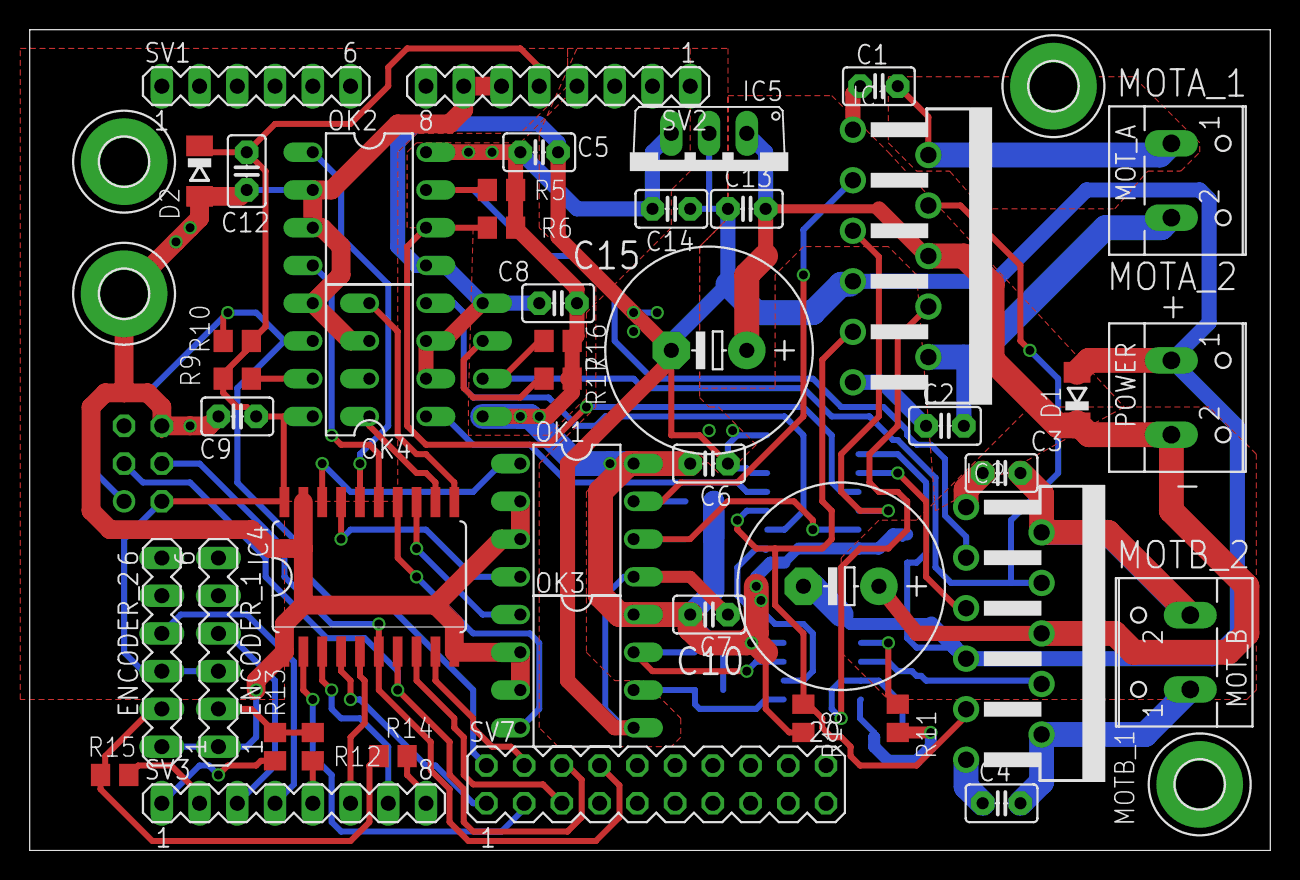
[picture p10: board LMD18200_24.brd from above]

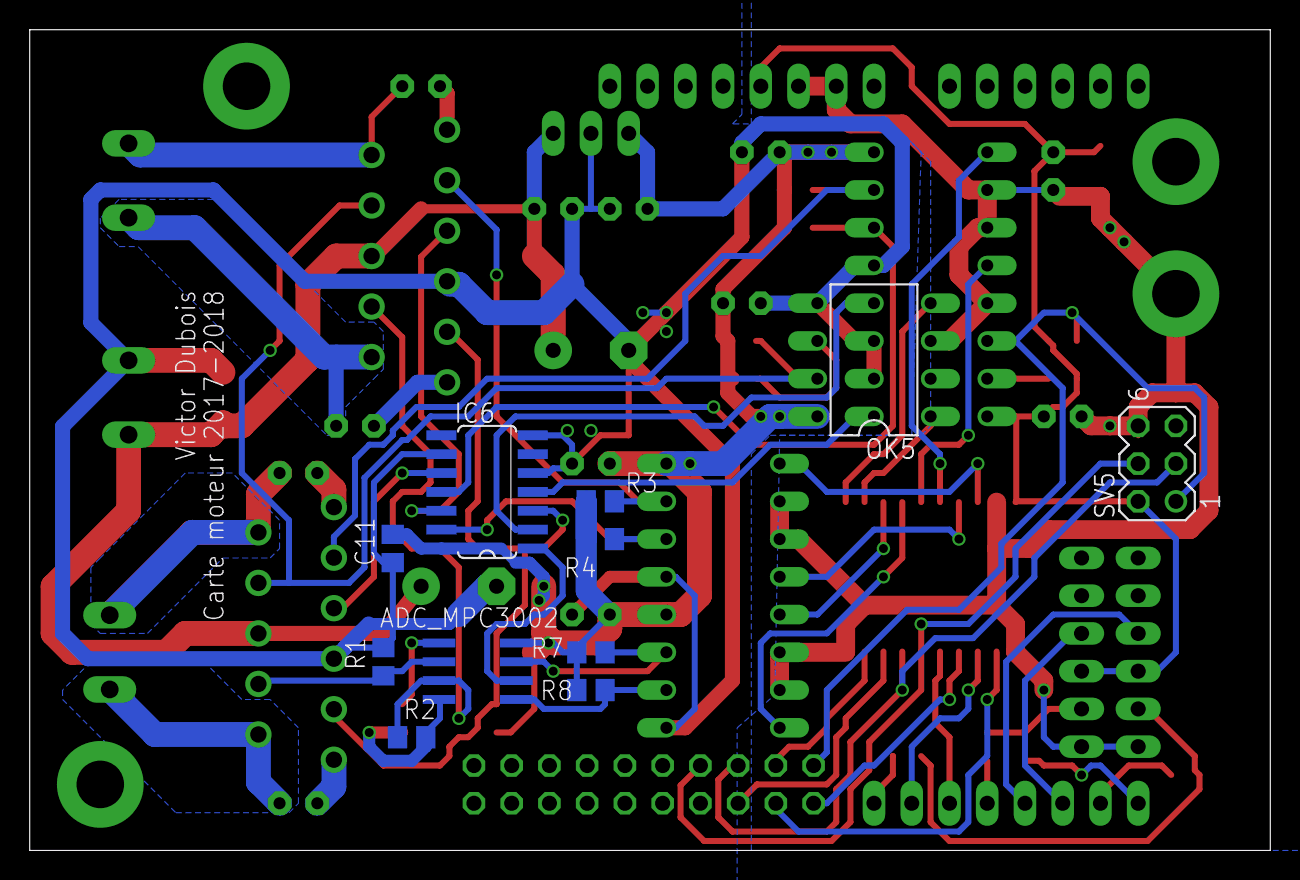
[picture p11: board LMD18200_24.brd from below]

Board: 2 copper layers, 83.5 x 55.2 mm, 60 parts (11 on the bottom side), 56 nets.

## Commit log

2018-03-22 close #1 creation
    [LMD18200_24.brd, LMD18200_24.ods, LMD18200_24.sch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]
2022-08-28 second board version
    [LMD18200_2_7_5.brd, LMD18200_2_7_5.sch]
2025-08-15 Add option 12V Elec + add missing brake pullups
    [DCDC_5V.kicad_sch, LMD18200.kicad_sch, motorBoardCan.kicad_pcb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]
2025-08-15 add choice between 12V power and 24V power
    [motorBoardCan.kicad_pcb, motorBoardCan.kicad_sch]
2026-06-20 Clarify PCB usage for Krabi V1 and V2
    Updated README to specify Krabi V1 and V2 PCB usage.
